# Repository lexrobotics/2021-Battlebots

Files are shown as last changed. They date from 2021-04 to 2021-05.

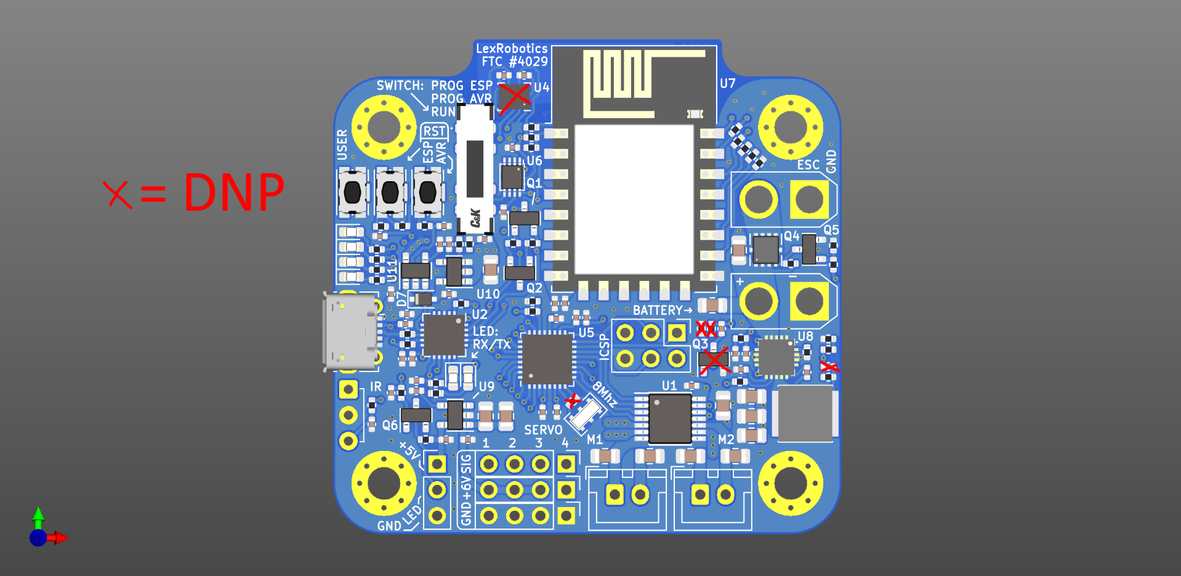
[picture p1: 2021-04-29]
BattlebotsController/BattlebotsController_AssembledView.png

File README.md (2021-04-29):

# 2021-Battlebots

Q: What am I looking at here?

A: 

📦2021-Battlebots \
 ┣ 📂BattlebotsController             `KiCAD files for the battlebots control board hardware` \
 ┣ 📂Code \
 ┃ ┣ 📂peripheralController           `Arduino code for the ATMEGA328P microcontroller` \
 ┃ ┗ 📂wifiController                 `Arduino code for the ESP8266 microcontroller` \
 ┗ 📂OLDVERSION-BattlebotsController  `KiCAD files for the old version of the control board`

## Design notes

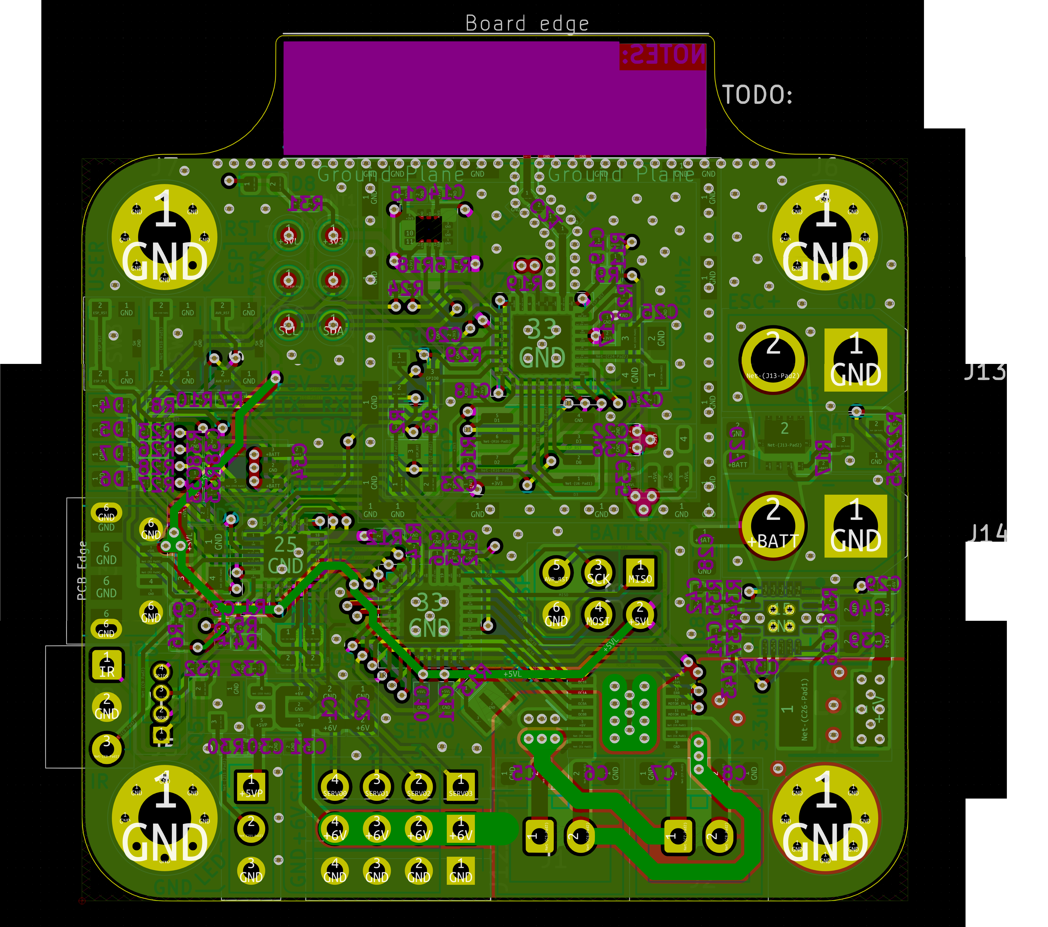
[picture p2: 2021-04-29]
OLDVERSION-BattlebotsController/bottomcopper.png

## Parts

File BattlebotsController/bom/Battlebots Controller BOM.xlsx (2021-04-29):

 | Source: | C:\Users\Anhad\Documents\Kicad\BattlebotsController\BattlebotsController.kicad_sch
 | Date: |  | 2021-04-04 23:49
 | Tool: | Eeschema (5.99.0-10089-gf88d39b4f0)
 | Generator: | C:\Program Files\KiCad\bin\scripting\plugins/bom_csv_grouped_by_value_with_fp.py
 | Component Count: | 149 |  |  |  |  |  |  |  | TOTAL: | 30.91
Item # | *Designator | *Qty | *Mfg Part # | Description / Value | Manufacturer | *Package/Footprint | NOTES | Digikey Part Number | Possible to substitute? | Price (1x) | Price Estimate
1 | C1, C2, C8, C9, C10, C11, C28, C29, C30, C31, C43, C46, C47, | 13 | CL21A106KOQNNNE | 10uf | Samsung Electromechanics | Capacitor_SMD:C_0805_2012Metric | Capacitors must all be >=10V | 1276-1096-1-ND | YES | 0.11 | 1.43
2 | C3, C4, C14, C15, C16, C23, C25, C27, C34, C35, C37, C39, C41, C45, | 14 | GRM155R61C105MA12D | 1uF | Murata Electronics | Capacitor_SMD:C_0402_1005Metric |  | 490-14599-1-ND | YES | 0.1 | 1.4
3 | C5, C6, C7, C17, C18, C19, C20, C21, C22, C24, C26, C32, | 12 | EMF105B7104KVHF | 0.1uF | Taiyo Yuden | Capacitor_SMD:C_0402_1005Metric |  | 587-6563-1-ND | YES | 0.1 | 1.2
4 | C12, C13, | 2 | CC0402GRNPO9BN470 | 47pF | Yageo | Capacitor_SMD:C_0402_1005Metric |  | 311-3741-1-ND | YES | 0.1 | 0.2
5 | C33, | 1 |  | NC |  | Capacitor_SMD:C_0402_1005Metric | DO NOT POPULATE |  |  |  | 0
6 | C36, C40, | 2 | CC0402JRX7R9BB471 | 470pF | Yageo | Capacitor_SMD:C_0402_1005Metric |  | 311-1679-1-ND | YES | 0.1 | 0.2
7 | C38, C44, | 2 | GRM155R71E223JA61D | 22nF | Murata Electronics | Capacitor_SMD:C_0402_1005Metric |  | 490-10699-1-ND | YES | 0.1 | 0.2
8 | C42, | 1 | CL05C390JB51PNC | 39pF | Samsung Electromechanics | Capacitor_SMD:C_0402_1005Metric |  | 1276-6863-1-ND | YES | 0.1 | 0.1
9 | C48, | 1 | CC0402JRX7R9BB392 | 3.9nF | Yageo | Capacitor_SMD:C_0402_1005Metric |  | 311-3771-1-ND | YES | 0.1 | 0.1
10 | D1, D2, D3, D4, D5, D6, | 6 | 150060VS75000 | LED 20mA, 2V | Würth Elektronik | LED_SMD:LED_0603_1608Metric | Green | 732-4980-1-ND | YES | 0.14 | 0.84
11 | D7, | 1 | PMEG4005EJ,115 | Schottky Diode | Nexperia USA Inc. | Diode_SMD:D_SOD-323F | < 0.5V voltage drop | 1727-3877-1-ND | YES | 0.31 | 0.31
12 | J3, | 1 | 1050170001 | USB_B_Micro | Molex | Connector_USB:USB_Micro-B_Molex-105017-0001 |  | WM1399CT-ND | NO | 0.83 | 0.83
13 | L1, | 1 | SRP5030CA-3R3M | 3.3uH | Bourns Incorporated | SRP5030CA:INDPM5355X310N | Shielded | SRP5030CA-3R3MCT-ND | NO | 1.65 | 1.65
14 | Q1, Q2, Q5, Q6, | 4 | MMSS8050-H-TP | S8050 | Micro Commercial Co. | Package_TO_SOT_SMD:SOT-23 | 0.7A Ic, 20V Vce, Low Voltage High Current NPN Transistor, TO-92 | MMSS8050-H-TPMSCT-ND | YES | 0.18 | 0.72
15 | Q3, | 1 | NC (S8050) | Q_NPN_BEC |  | Package_TO_SOT_SMD:SOT-23 | DO NOT POPULATE |  | YES
16 | Q4, | 1 | AONR21307 | P-MOSFET transistor, gate/drain/source | Alpha & Omega Semiconductor | AONR21307:TRANS_AONR21321 |  | 785-1796-1-ND | YES | 0.56 | 0.56
17 | R1, R2, R5, R6, R12, R13, R15, R23, R24, R25, R26, R29, R30, R31, R33, R40, | 16 | RC0402FR-0712KL | 12k | Yageo | Resistor_SMD:R_0402_1005Metric |  | 311-12.0KLRCT-ND | YES | 0.1 | 1.6
18 | R3, R4, R28, R32, R34, | 5 | CRCW0402470RFKEDC | 470 | Vishay Dale | Resistor_SMD:R_0402_1005Metric |  | 541-4072-1-ND | YES | 0.1 | 0.5
19 | R7, R8, | 2 | AC0402FR-0727RL | 27 | Yageo | Resistor_SMD:R_0402_1005Metric |  | YAG5278CT-ND | YES
20 | R9, R10, R11, R14, R16, R18, R19, | 7 | RC0402FR-07270RL | 270 | Yageo | Resistor_SMD:R_0402_1005Metric |  | 311-270LRCT-ND | YES | 0.1 | 0.7
21 | R17, R20, R22, | 3 |  | NC |  | Resistor_SMD:R_0402_1005Metric | DO NOT POPULATE
22 | R21, R35, | 2 | CRCW040218K0FKED | 18k | Vishay Dale | Resistor_SMD:R_0402_1005Metric |  | 541-18.0KLCT-ND | YES | 0.1 | 0.2
23 | R27, R36, R41, | 3 | CRCW04021K00FKEDC | 1k | Vishay Dale | Resistor_SMD:R_0402_1005Metric |  | 541-3961-1-ND | YES | 0.1 | 0.3
24 | R37, | 1 | RC0402FR-0743KL | 43k | Yageo | Resistor_SMD:R_0402_1005Metric |  | 311-43.0KLRCT-ND | YES | 0.1 | 0.1
25 | R38, | 1 | RC0402DR-07100KL | 100k | Yageo | Resistor_SMD:R_0402_1005Metric |  | 13-RC0402DR-07100KLCT-ND | YES | 0.1 | 0.1
26 | R39, | 1 | CRCW04024K64FKED | 4.64k | Vishay Dale | Resistor_SMD:R_0402_1005Metric |  | 541-4.64KLCT-ND | YES | 0.1 | 0.1
27 | SW1, SW2, SW3, | 3 | KMR221GLFS | SPST BUTTON | C&K | Button_Switch_SMD:SW_Push_1P1T-SH_NO_CK_KMR2xxG |  | 401-1427-1-ND | NO | 0.48 | 1.44
28 | SW4, | 1 | JS203011JCQN | DP3T SLIDE | C&K | BattlebotsController:JS203011JCQN | Switch, three position, double pole triple throw, 3 position switch, SP3T | CKN10725CT-ND | NO | 0.65 | 0.65
29 | U1, | 1 | TLE94004EP | Motor Driver | Infineon | Package_SO:Infineon_PG-TSDSO-14-22 |  | TLE94004EPXUMA1CT-ND | NO | 2.07 | 2.07
30 | U2, | 1 | FT231XQ | USB - UART | FTDI, Future Technology Devices International Ltd | Package_DFN_QFN:QFN-20-1EP_4x4mm_P0.5mm_EP2.5x2.5mm | Full Speed USB to Full Handshake UART, QFN-20 | 768-1155-ND | NO | 2.22 | 2.22
31 | U4, | 1 | LSM6DSM | LSM6DSx | STMicroelectronics | Package_LGA:LGA-14_3x2.5mm_P0.5mm_LayoutBorder3x4y | DO NOT POPULATE | 497-16696-1-ND | YES | 2.92 | 2.92
32 | U5, | 1 | ATmega328P-MU | 20MHz, 32kB Flash, 2kB SRAM, 1kB EEPROM, QFN-32 | Microchip Technology | Package_DFN_QFN:QFN-32-1EP_5x5mm_P0.5mm_EP3.1x3.1mm |  | ATMEGA328P-MU-ND | NO | 2.01 | 2.01
33 | U6, | 1 | TXB0102DCU | Level Shifter | Texas Instruments | Package_SO:VSSOP-8_2.4x2.1mm_P0.5mm | 2-Bit Bidirectional Voltage-Level Translator in VSSOP Package With Auto Direction Sensing and ±15-kV ESD Protection | 296-22862-1-ND | NO | 0.76 | 0.76
34 | U7, | 1 | ESP-12F | ESP8266 Module | Ai-Thinker | RF_Module:ESP-12E/F | 802.11 b/g/n Wi-Fi Module |  | NO* |  | 0
35 | U8, | 1 | TPS54821RHLR | 8A Buck Converter | Texas Instruments | TPS54821:IC_TPS54821RHLR |  | 296-29744-1-ND | NO | 2.92 | 2.92
36 | U9, | 1 | MIC5219-5.0YM5 | FIXED 5V!!!! | Microchip Technology | Package_TO_SOT_SMD:SOT-23-5 | 500mA low dropout linear regulator, fixed 5.0V output, SOT-23-5 | 576-2770-1-ND | YES | 0.89 | 0.89
37 | U10, | 1 | SPX3819M5-L | ADJUSTABLE!!!! | MaxLinear Incorporated | Package_TO_SOT_SMD:SOT-23-5 | 500mA Low drop-out regulator, Adjustable, SOT-23-5 | 1016-1873-1-ND | NO | 0.49 | 0.49
38 | U11, | 1 | MIC5219-3.3YM5 | FIXED 3.3V!!!! | Microchip Technology | Package_TO_SOT_SMD:SOT-23-5 | 500mA low dropout linear regulator, fixed 3.3V output, SOT-23-5 | 576-1281-1-ND | YES | 0.93 | 0.93
39 | Y1, | 1 | CSTNE16M0V530000R0 | 16M resonator | Murata Electronics | Crystal:Resonator_SMD_muRata_CSTxExxV-3Pin_3.0x1.1mm | Three pin ceramic resonator | 490-17948-1-ND | YES | 0.27 | 0.27
40
41
42
 | NOT POPULATED / THRU HOLE | PCBWAY - IGNORE
Item # | *Designator | *Qty | *Mfg Part # | Description / Value | Manufacturer | *Package/Footprint | NOTES | Digikey Part Number | Possible to substitute with another equivalent part? | Price (1x) | Unit Price
43 | TP1, TP2, TP3, TP4, TP5, TP6, TP7, TP8, TP9, TP10, TP11, TP12, TP13, | 13 |  | TestPoint_Flag | TestPoint_Flag | TestPoint:TestPoint_Pad_D1.5mm | DO NOT POPULATE
44 | JP1, JP2, JP3, | 3 |  | Jumper_NC_Small | Jumper_NC_Small | Jumper:SolderJumper-2_P1.3mm_Bridged_RoundedPad1.0x1.5mm | DO NOT POPULATE
45 | MH1, MH2, MH3, MH4, | 4 |  | MOUNTING_HOLE | Conn_01x01 | MountingHole:MountingHole_3.2mm_M3_Pad_Via | DO NOT POPULATE
46 | J4, | 1 |  | ICSP | Conn_02x03_Odd_Even | Connector_PinHeader_2.54mm:PinHeader_2x03_P2.54mm_Vertical | DO NOT POPULATE
47 | J5, | 1 |  | SIG | Conn_01x04 | Connector_PinHeader_2.54mm:PinHeader_1x04_P2.54mm_Vertical | DO NOT POPULATE
48 | J6, | 1 |  | +6V | Conn_01x04 | Connector_PinHeader_2.54mm:PinHeader_1x04_P2.54mm_Vertical | DO NOT POPULATE
49 | J7, | 1 |  | GND | Conn_01x04 | Connector_PinHeader_2.54mm:PinHeader_1x04_P2.54mm_Vertical | DO NOT POPULATE
50 | J8, | 1 |  | ESC | Conn_01x02 | Connector_AMASS:AMASS_XT30U-M_1x02_P5.0mm_Vertical | DO NOT POPULATE
51 | J9, | 1 |  | BATTERY | Conn_01x02 | Connector_AMASS:AMASS_XT30U-M_1x02_P5.0mm_Vertical | DO NOT POPULATE
52 | J10, | 1 |  | WS2812b | Conn_01x03 | Connector_PinHeader_2.54mm:PinHeader_1x03_P2.54mm_Vertical | DO NOT POPULATE
53 | J1, | 1 | B2B-XH-A-M(LF)(SN) | DRIVE_MOTOR_R | Conn_01x02 | Connector_JST:JST_XH_B2B-XH-A_1x02_P2.50mm_Vertical | DO NOT POPULATE
54 | J2, | 1 | B2B-XH-A-M(LF)(SN) | DRIVE_MOTOR_L | Conn_01x02 | Connector_JST:JST_XH_B2B-XH-A_1x02_P2.50mm_Vertical | DO NOT POPULATE
55 | U3, | 1 | TSOP382xx | TSOP382xx | OptoDevice:Vishay_MINICAST-3Pin | Photo Modules for PCM Remote Control Systems | DO NOT POPULATE |  | YES
56
57
58 | TOTAL NC/THRU-HOLE PARTS | 30
59
60

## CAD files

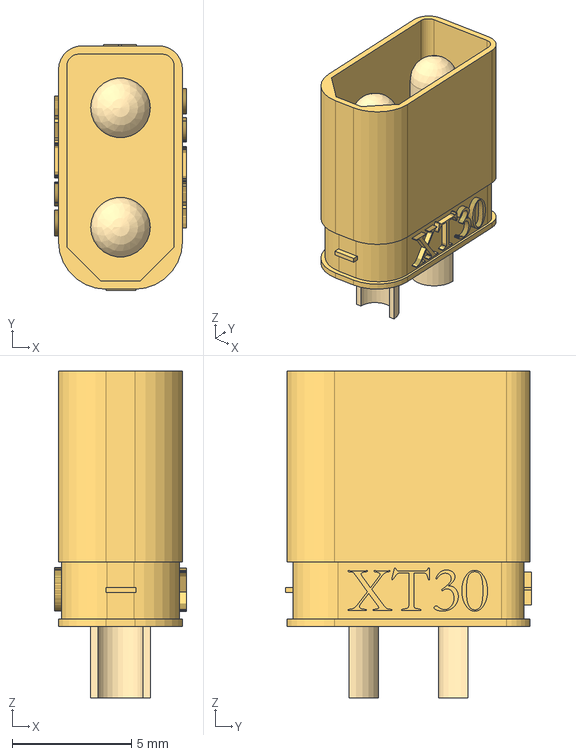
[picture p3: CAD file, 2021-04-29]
BattlebotsController/3D/XT30-male.step
5.54 x 10.3 x 13.7 mm

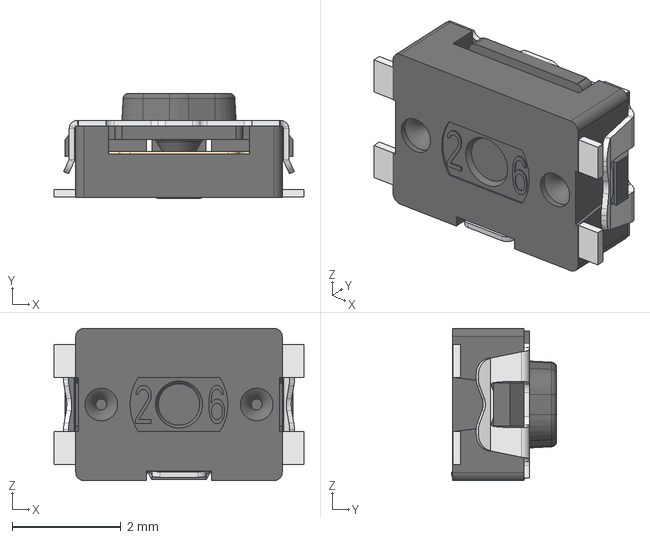
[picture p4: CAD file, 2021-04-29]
BattlebotsController/3D/KMR211GLFS.step
4.60 x 1.94 x 2.80 mm

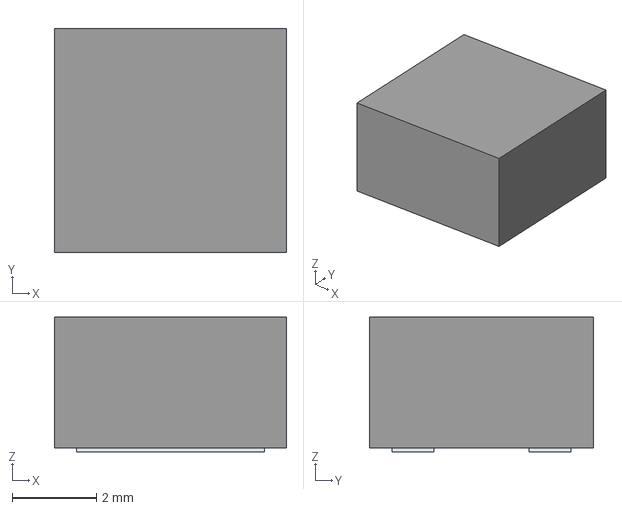
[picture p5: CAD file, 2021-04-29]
BattlebotsController/3D/SRP5030CA.stp
5.50 x 5.30 x 3.20 mm
Pins

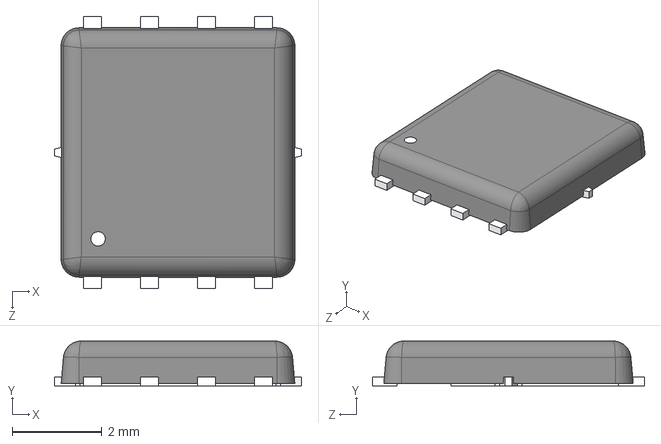
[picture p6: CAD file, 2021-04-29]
BattlebotsController/3D/MOSFET_AONR.STEP
5.50 x 1.00 x 6.05 mm

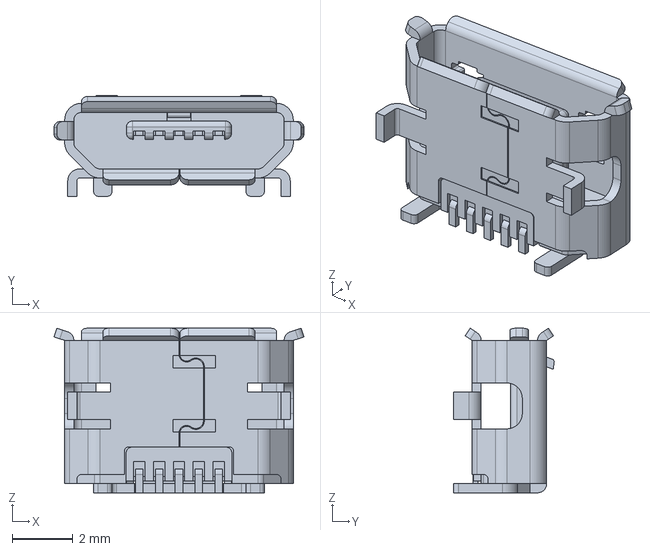
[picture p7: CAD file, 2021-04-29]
BattlebotsController/3D/Molex_1050170001.stp
8.20 x 3.30 x 5.40 mm

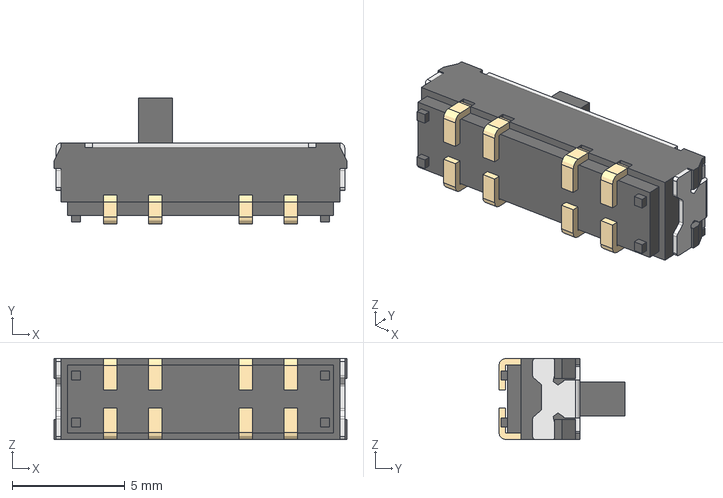
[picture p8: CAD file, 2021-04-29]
BattlebotsController/3D/JS203011JCQN.step
13.0 x 5.60 x 3.60 mm

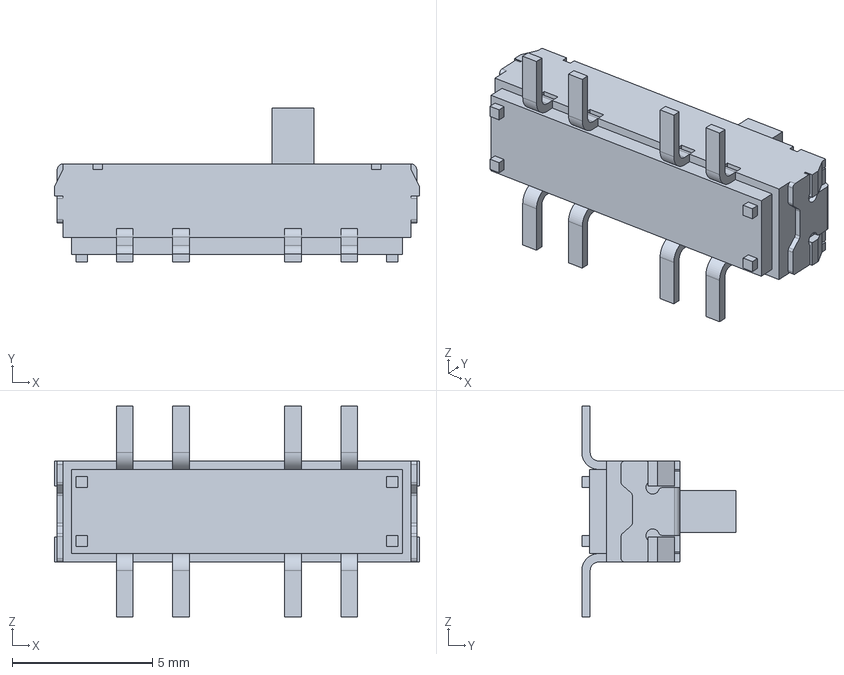
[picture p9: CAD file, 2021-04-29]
BattlebotsController/3D/JS203011SCQN.stp
13.0 x 5.50 x 7.50 mm

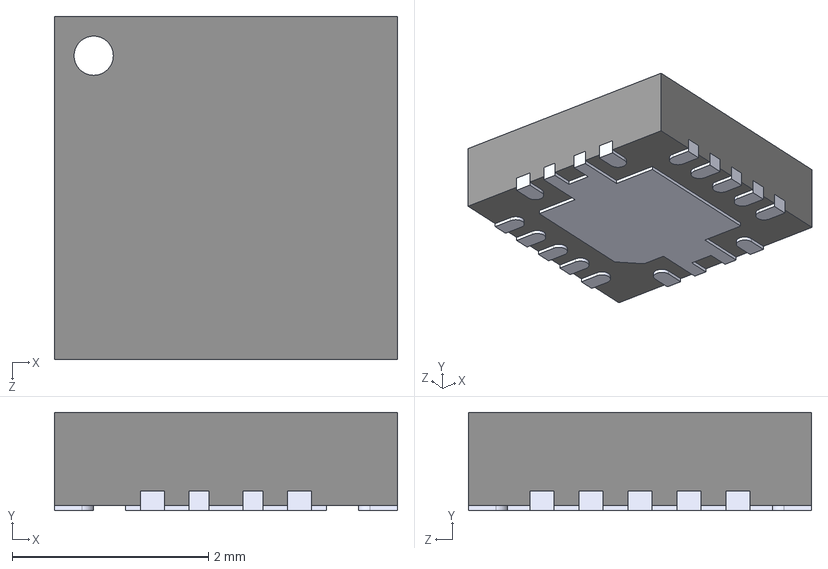
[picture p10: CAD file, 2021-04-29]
BattlebotsController/3D/TPS54821RHLR--3DModel-STEP-56544.STEP
3.50 x 1.00 x 3.50 mm

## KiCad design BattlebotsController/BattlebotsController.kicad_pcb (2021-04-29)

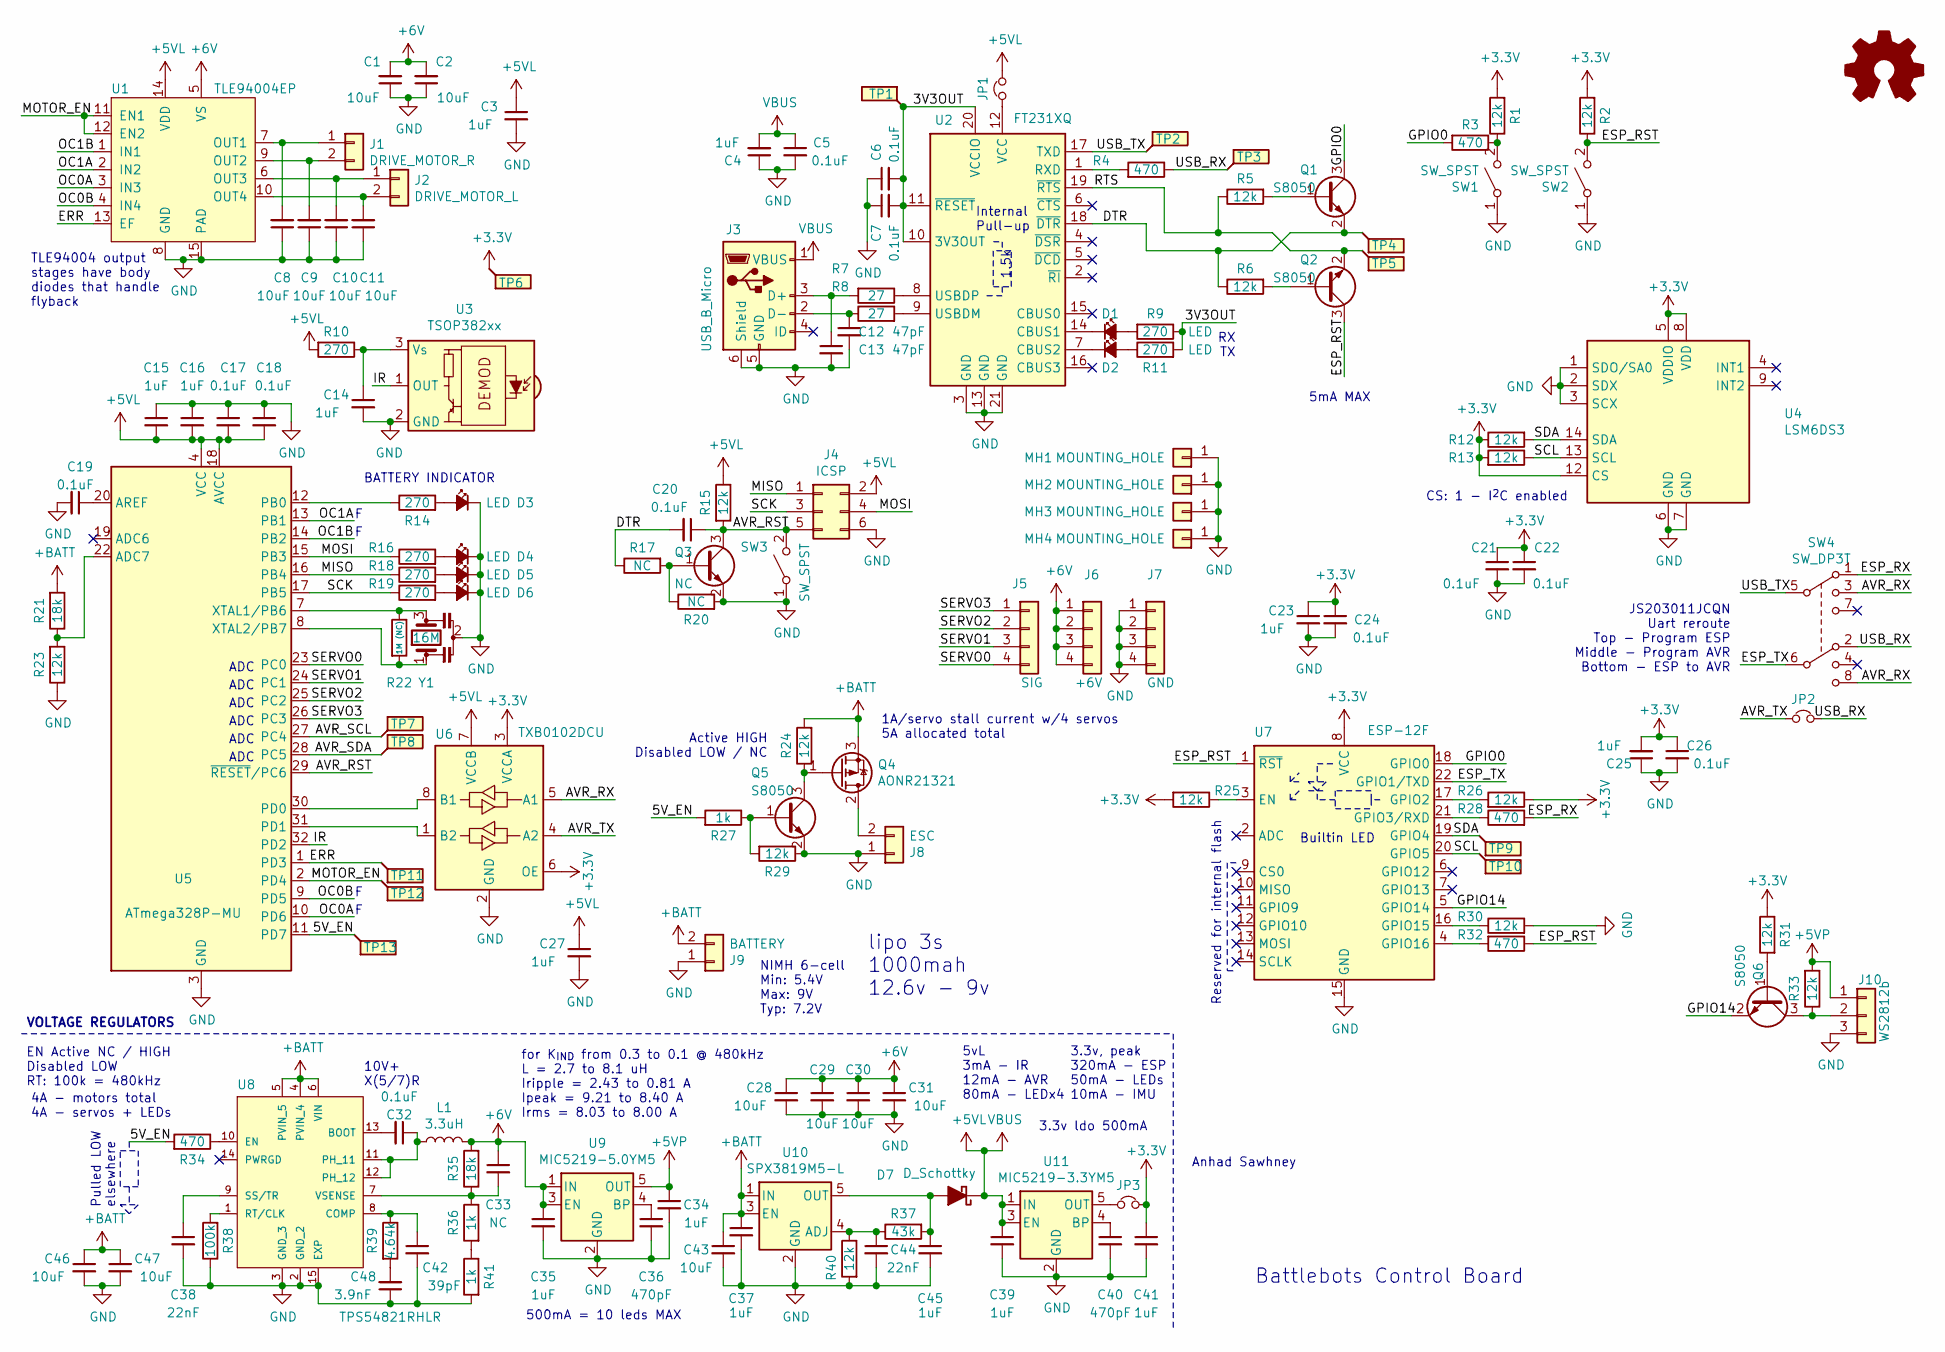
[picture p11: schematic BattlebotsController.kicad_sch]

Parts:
C1, C2, C8, C9, C10, C11, C28, C29, C30, C31, C43, C46, C47: 10uF; C_0805_2012Metric
C3, C4, C14, C15, C16, C23, C25, C27, C34, C35, C37, C39, C41, C45: 1uF; C_0402_1005Metric
C5, C6, C7, C17, C18, C19, C20, C21, C22, C24, C26, C32: 0.1uF; C_0402_1005Metric
C12, C13: 47pF; C_0402_1005Metric
C33: NC; C_0402_1005Metric
C36, C40: 470pF; C_0402_1005Metric
C38, C44: 22nF; C_0402_1005Metric
C42: 39pF; C_0402_1005Metric
C48: 3.9nF; C_0402_1005Metric
D1, D2, D3, D4, D5, D6: LED; LED_0603_1608Metric
D7: D_Schottky; D_SOD-323F
J1: DRIVE_MOTOR_R; JST_XH_B2B-XH-A_1x02_P2.50mm_Vertical
J2: DRIVE_MOTOR_L; JST_XH_B2B-XH-A_1x02_P2.50mm_Vertical
J3: USB_B_Micro; USB_Micro-B_Molex-105017-0001
J4: ICSP; PinHeader_2x03_P2.54mm_Vertical
J5: SIG; PinHeader_1x04_P2.54mm_Vertical
J6: +6V; PinHeader_1x04_P2.54mm_Vertical
J7: GND; PinHeader_1x04_P2.54mm_Vertical
J8: ESC; AMASS_XT30U-M_1x02_P5.0mm_Vertical
J9: BATTERY; AMASS_XT30U-M_1x02_P5.0mm_Vertical
J10: WS2812b; PinHeader_1x03_P2.54mm_Vertical
JP1, JP2, JP3: Jumper_NC_Small; SolderJumper-2_P1.3mm_Bridged_RoundedPad1.0x1.5mm
L1: 3.3uH; INDPM5355X310N
MH1, MH2, MH3, MH4: MOUNTING_HOLE; MountingHole_3.2mm_M3_Pad_Via
Q1, Q2, Q5, Q6: S8050; SOT-23
Q3: NC; SOT-23
Q4: AONR21321; TRANS_AONR21321
R1, R2, R5, R6, R12, R13, R15, R23, R24, R25, R26, R29, R30, R31, R33, R40: 12k; R_0402_1005Metric
R3, R4, R28, R32, R34: 470; R_0402_1005Metric
R7, R8: 27; R_0402_1005Metric
R9, R10, R11, R14, R16, R18, R19: 270; R_0402_1005Metric
R17, R20: NC; R_0402_1005Metric
R21, R35: 18k; R_0402_1005Metric
R22: 1M (NC); R_0402_1005Metric
R27, R36, R41: 1k; R_0402_1005Metric
R37: 43k; R_0402_1005Metric
R38: 100k; R_0402_1005Metric
R39: 4.64k; R_0402_1005Metric
SW1, SW2, SW3: SW_SPST; SW_Push_1P1T-SH_NO_CK_KMR2xxG
SW4: SW_DP3T; JS203011JCQN
TP1, TP2, TP3, TP4, TP5, TP6, TP7, TP8, TP9, TP10, TP11, TP12, TP13: TestPoint_Flag; TestPoint_Pad_D1.5mm
U1: TLE94004EP; Infineon_PG-TSDSO-14-22
U2: FT231XQ; QFN-20-1EP_4x4mm_P0.5mm_EP2.5x2.5mm
U3: TSOP382xx; Vishay_MINICAST-3Pin
U4: LSM6DS3; LGA-14_3x2.5mm_P0.5mm_LayoutBorder3x4y
U5: ATmega328P-MU; QFN-32-1EP_5x5mm_P0.5mm_EP3.1x3.1mm
U6: TXB0102DCU; VSSOP-8_2.4x2.1mm_P0.5mm
U7: ESP-12F; ESP-12E
U8: TPS54821RHLR; IC_TPS54821RHLR
U9: MIC5219-5.0YM5; SOT-23-5
U10: SPX3819M5-L; SOT-23-5
U11: MIC5219-3.3YM5; SOT-23-5
Y1: 16M; Resonator_SMD_Murata_CSTxExxV-3Pin_3.0x1.1mm

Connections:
+3V3: C21.1, C22.1, C23.1, C24.1, C25.2, C26.1, C41.1, JP3.2, R1.2, R2.2, R12.1, R13.2, R25.2, R26.1, R31.1, TP6.1, U4.5 (VDDIO), U4.8 (VDD), U4.12 (CS), U6.3 (VCCA), U6.6 (OE), U7.8 (VCC)
+5VL: C3.1, C4.2, C5.1, C15.2, C16.2, C17.2, C18.2, C27.1, C39.1, D7.1 (K), J3.1 (VBUS), J4.2, JP1.2, R10.2, R15.1, U1.14 (VDD), U5.4 (VCC), U5.6 (VCC), U5.18 (AVCC), U6.7 (VCCB), U11.1 (IN), U11.3 (EN)
+5VP: C34.1, J10.1, R33.2, U9.5 (OUT)
+6V: C1.2, C2.2, C28.1, C29.1, C30.1, C31.1, C33.1, C35.1, J6.1, J6.2, J6.3, J6.4, L1.2, R35.2, U1.5 (VS), U9.1 (IN), U9.3 (EN)
+BATT: C37.1, C43.1, C46.1, C47.1, J9.2, Q4.3 (S), R21.2, R24.2, U8.4 (PVIN_4), U8.5 (PVIN_5), U8.6 (VIN), U10.1 (IN), U10.3 (EN)
/3V3OUT: C6.2, C7.2, R9.1, R11.2, TP1.1, U2.10 (3V3OUT), U2.11 (~RESET), U2.20 (VCCIO)
/5V_EN: R27.2, R34.2, TP13.1, U5.11 (PD7)
/AVR_RST: C20.1, J4.5, Q3.3 (C), R15.2, SW3.2 (B), U5.29 (~RESET~/PC6)
/AVR_RX: SW4.3, SW4.8, U6.5 (A1)
/AVR_SCL: TP7.1, U5.27 (PC4)
/AVR_SDA: TP8.1, U5.28 (PC5)
/AVR_TX: JP2.1, U6.4 (A2)
/DTR: C20.2, Q1.2 (E), R6.1, R17.1, TP4.1, U2.18 (~DTR)
/ERR: TP11.1, U1.13 (EF), U5.1 (PD3)
/ESP_RST: Q2.3 (C), R2.1, R32.1, SW2.2 (B), U7.1 (~RST)
/ESP_RX: R28.2, SW4.1
/ESP_TX: SW4.6, U7.22 (GPIO1/TXD)
/GPIO0: Q1.3 (C), R3.2, U7.18 (GPIO0)
/GPIO14: Q6.2 (E), U7.5 (GPIO14)
/IR: U3.1 (OUT), U5.32 (PD2)
/MISO: J4.1, R18.1, U5.16 (PB4)
/MOSI: J4.4, R16.1, U5.15 (PB3)
/MOTOR_EN: TP12.1, U1.11 (EN1), U1.12 (EN2), U5.2 (PD4)
/OC0A: U1.3 (IN3), U5.10 (PD6)
/OC0B: U1.4 (IN4), U5.9 (PD5)
/OC1A: U1.2 (IN2), U5.13 (PB1)
/OC1B: U1.1 (IN1), U5.14 (PB2)
/RTS: Q2.2 (E), R5.1, TP5.1, U2.19 (~RTS)
/SCK: J4.3, R19.1, U5.17 (PB5)
/SCL: R13.1, TP10.1, U4.13 (SCL), U7.20 (GPIO5)
/SDA: R12.2, TP9.1, U4.14 (SDA), U7.19 (GPIO4)
/SERVO0: J5.4, U5.23 (PC0)
/SERVO1: J5.3, U5.24 (PC1)
/SERVO2: J5.2, U5.25 (PC2)
/SERVO3: J5.1, U5.26 (PC3)
/USB_RX: JP2.2, R4.1, SW4.2, TP3.1
/USB_TX: SW4.5, TP2.1, U2.17 (TXD)
GND: C1.1, C2.1, C3.2, C4.1, C5.2, C6.1, C7.1, C8.1, C9.1, C10.1, C11.1, C12.2, C13.2, C14.2, C15.1, C16.1, C17.1, C18.1, C19.2, C21.2, C22.2, C23.2, C24.2, C25.1, C26.2, C27.2, C28.2, C29.2, C30.2, C31.2, C34.2, C35.2, C36.2, C37.2, C38.2, C39.2, C40.2, C41.2, C42.2, C43.2, C44.2, C45.2, C46.2, C47.2, C48.1, D3.1 (K), D4.1 (K), D5.1 (K), D6.1 (K), J3.5 (GND), J3.6 (Shield), J4.6, J7.1, J7.2, J7.3, J7.4, J8.1, J9.1, J10.3, MH1.1, MH2.1, MH3.1, MH4.1, Q3.2 (E), Q5.2 (E), R20.2, R23.1, R29.1, R30.2, R38.1, R40.2, R41.2, SW1.1 (A), SW2.1 (A), SW3.1 (A), U1.8 (GND), U1.15 (PAD), U2.3 (GND), U2.13 (GND), U2.21 (GND), U3.2 (GND), U4.1 (SDO/SA0), U4.2 (SDX), U4.3 (SCX), U4.6 (GND), U4.7 (GND), U5.3 (GND), U5.5 (GND), U5.21 (GND), U5.33 (GND), U6.2 (GND), U7.15 (GND), U8.2 (GND_2), U8.3 (GND_3), U8.15 (EXP), U9.2 (GND), U10.2 (GND), U11.2 (GND), Y1.2
unnamed: C8.2, J1.1, U1.7 (OUT1)
unnamed: C9.2, J1.2, U1.9 (OUT2)
unnamed: C10.2, J2.1, U1.6 (OUT3)
unnamed: C11.2, J2.2, U1.10 (OUT4)
unnamed: C12.1, J3.2 (D-), R8.1
unnamed: C13.1, J3.3 (D+), R7.2
unnamed: C19.1, U5.20 (AREF)
unnamed: C32.1, L1.1, U8.11 (PH_11), U8.12 (PH_12)
unnamed: C32.2, U8.13 (BOOT)
unnamed: C33.2, R35.1, R36.1, U8.7 (VSENSE)
unnamed: C36.1, U9.4 (BP)
unnamed: C38.1, U8.9 (SS/TR)
unnamed: C40.1, U11.4 (BP)
unnamed: C42.1, R39.1, U8.8 (COMP)
unnamed: C44.1, R37.1, R40.1, U10.4 (ADJ)
unnamed: C45.1, D7.2 (A), R37.2, U10.5 (OUT)
unnamed: C48.2, R39.2
unnamed: D1.1 (K), U2.14 (CBUS1)
unnamed: D1.2 (A), R9.2
unnamed: D2.1 (K), U2.7 (CBUS2)
unnamed: D2.2 (A), R11.1
unnamed: D3.2 (A), R14.2
unnamed: D4.2 (A), R16.2
unnamed: D5.2 (A), R18.2
unnamed: D6.2 (A), R19.2
unnamed: J8.2, Q4.2 (D)
unnamed: J10.2, Q6.3 (C), R33.1
unnamed: JP1.1, U2.12 (VCC)
unnamed: JP3.1, U11.5 (OUT)
unnamed: Q1.1 (B), R5.2
unnamed: Q2.1 (B), R6.2
unnamed: Q3.1 (B), R17.2, R20.1
unnamed: Q4.1 (G), Q5.3 (C), R24.1
unnamed: Q5.1 (B), R27.1, R29.2
unnamed: Q6.1 (B), R31.2
unnamed: R1.1, R3.1, SW1.2 (B)
unnamed: R4.2, U2.1 (RXD)
unnamed: R7.1, U2.8 (USBDP)
unnamed: R8.2, U2.9 (USBDM)
unnamed: C14.1, R10.1, U3.3 (Vs)
unnamed: R14.1, U5.12 (PB0)
unnamed: R21.1, R23.2, U5.22 (ADC7)
unnamed: R22.1, U5.7 (XTAL1/PB6), Y1.3
unnamed: R22.2, U5.8 (XTAL2/PB7), Y1.1
unnamed: R25.1, U7.3 (EN)
unnamed: R26.2, U7.17 (GPIO2)
unnamed: R28.1, U7.21 (GPIO3/RXD)
unnamed: R30.1, U7.16 (GPIO15)
unnamed: R32.2, U7.4 (GPIO16)
unnamed: R34.1, U8.10 (EN)
unnamed: R36.2, R41.1
unnamed: R38.2, U8.1 (RT/CLK)
unnamed: U5.30 (PD0), U6.8 (B1)
unnamed: U5.31 (PD1), U6.1 (B2)

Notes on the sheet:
VOLTAGE REGULATORS
EN Active NC / HIGH Disabled LOW RT: 100k = 480kHz
TLE94004 output stages have body diodes that handle flyback
4A - motors total 4A - servos + LEDs
Pulled LOW elsewhere
ADC
BATTERY INDICATOR
10V+ X(5/7)R
for K_{IND} from 0.3 to 0.1 @ 480kHz L = 2.7 to 8.1 uH Iripple = 2.43 to 0.81 A Ipeak = 9.21 to 8.40 A Irms = 8.03 to 8.00 A
500mA = 10 leds MAX
NIMH 6-cell Min: 5.4V Max: 9V Typ: 7.2V
Active HIGH Disabled LOW / NC
lipo 3s 1000mah 12.6v - 9v
1A/servo stall current w/4 servos 5A allocated total
5vL 3mA - IR 12mA - AVR 80mA - LEDx4
Internal Pull-up
1.5k
3.3v ldo 500mA
3.3v, peak 320mA - ESP 50mA - LEDs 10mA - IMU
Anhad Sawhney
RX TX
Reserved for internal flash
Battlebots Control Board
Builtin LED
5mA MAX
CS: 1 - I^{2}C enabled
JS203011JCQN Uart reroute Top - Program ESP Middle - Program AVR Bottom - ESP to AVR

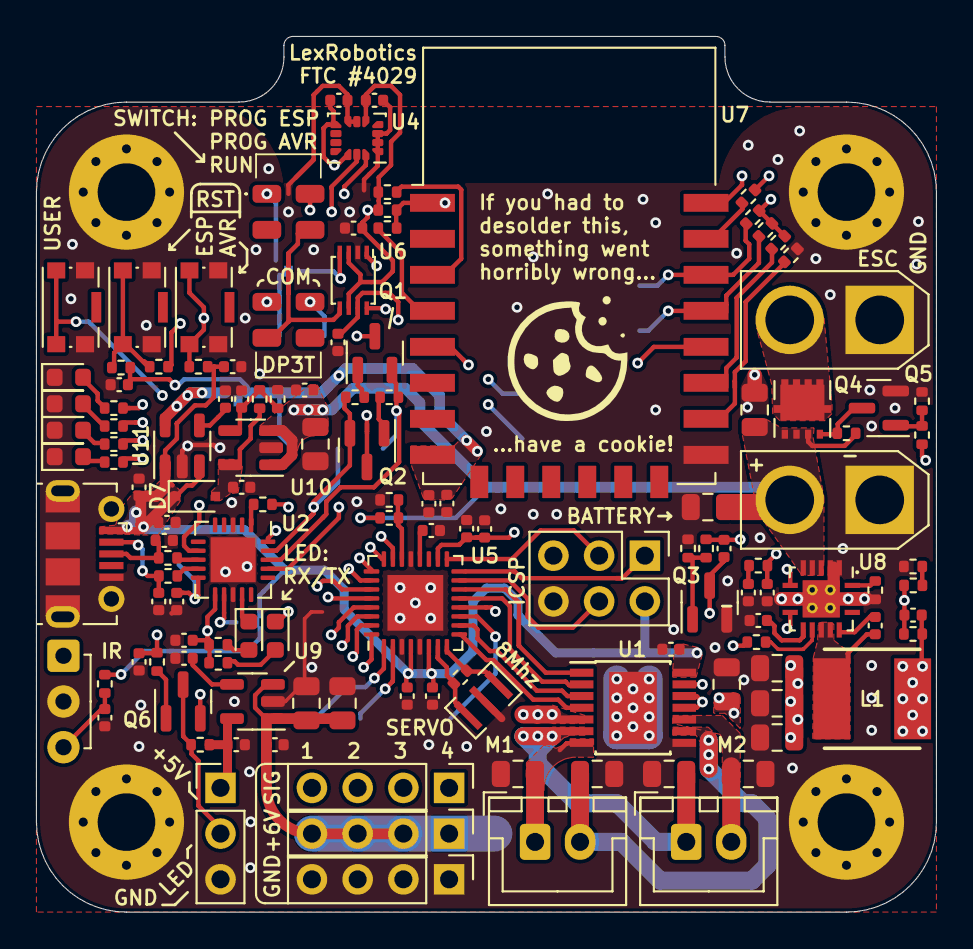
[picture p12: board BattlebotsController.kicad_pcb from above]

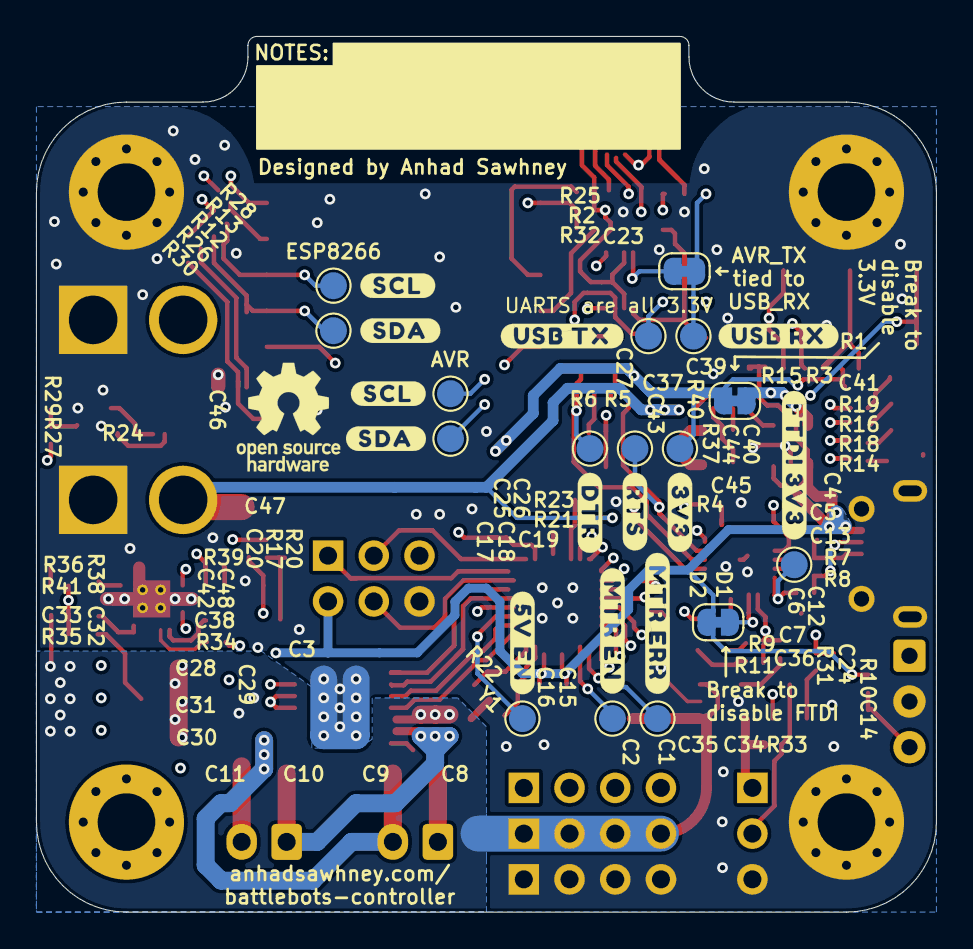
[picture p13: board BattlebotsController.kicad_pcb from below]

Board: 4 copper layers, 50.0 x 48.6 mm, 149 parts (16 on the bottom side), 92 nets.

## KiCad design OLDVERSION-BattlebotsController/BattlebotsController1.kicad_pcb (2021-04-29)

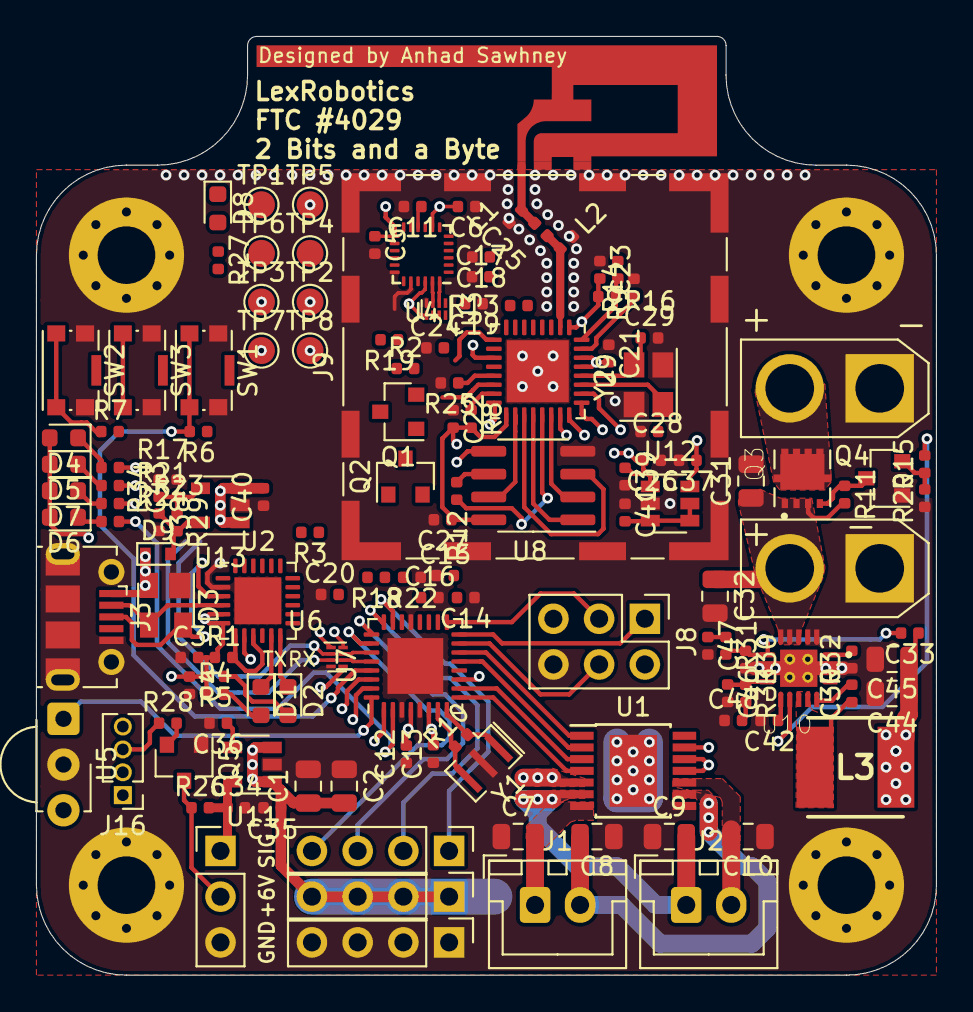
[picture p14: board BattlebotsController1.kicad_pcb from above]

Board: 4 copper layers, 50.0 x 52.1 mm, 142 parts (0 on the bottom side), 96 nets.

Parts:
ANT1: Inverted F; SWRU120B
C1, C2: 10uf; C_0805_2012Metric
C3, C26, C37, C39: 1uF; C_0402_1005Metric
C4, C5, C6, C11, C17, C18, C19, C20, C27: 0.1uF; C_0402_1005Metric
C7, C8, C9, C10, C31, C32, C44, C45: 10uF; C_0805_2012Metric
C12, C13, C21, C22, C41: 1uf; C_0402_1005Metric
C14, C15, C16, C23, C24: 0.1uf; C_0402_1005Metric
C25: 5.6pf; C_0402_1005Metric
C28, C29: NC; C_0402_1005Metric
C30, C42: 10uF; C_0402_1005Metric
C33, C35, C47: 330pf; C_0402_1005Metric
C34, C38, C40: 2.2uf; C_0402_1005Metric
C36, C43: 470pf; C_0402_1005Metric
C46: 14pf; C_0402_1005Metric
C48: 33nf; C_0402_1005Metric
D1: RXLED; LED_0603_1608Metric
D2: TXLED; LED_0603_1608Metric
D3: SP0503BAHT; SOT-143
D4, D5, D6, D7: LED; LED_0603_1608Metric
D8: ESP_LED; LED_0603_1608Metric
D9: MSK4005; D_SOD-523
J1: DRIVE_MOTOR_R; JST_XH_B2B-XH-A_1x02_P2.50mm_Vertical
J2: DRIVE_MOTOR_L; JST_XH_B2B-XH-A_1x02_P2.50mm_Vertical
J3: USB_B_Micro; USB_Micro-B_Molex-105017-0001
J4, J5, J6, J7: MOUNTING_HOLE; MountingHole_3.2mm_M3_Pad_Via
J8: ICSP; PinHeader_2x03_P2.54mm_Vertical
J9: RF_SHIELD; Wuerth_36103205_20x20mm
J10: SIG; PinHeader_1x04_P2.54mm_Vertical
J11: +6V; PinHeader_1x04_P2.54mm_Vertical
J12: GND; PinHeader_1x04_P2.54mm_Vertical
J13: ESC; AMASS_XT30U-M_1x02_P5.0mm_Vertical
J14: BATTERY; AMASS_XT30U-M_1x02_P5.0mm_Vertical
J15: WS2812b; PinHeader_1x03_P2.54mm_Vertical
J16: LED_DMA; PinHeader_1x04_P1.27mm_Vertical
L1, L2: NC; L_0402_1005Metric
L3: 3.3uH; INDPM5355X310N
Q1, Q2, Q4, Q5: S8050; SOT-23
Q3: Q_PMOS_GDS; TRANS_AONR21321
R1, R15: 1k; R_0402_1005Metric
R2, R3, R6, R7, R8, R11, R13, R14, R16, R20, R25, R28: 12k; R_0402_1005Metric
R4, R5, R17, R21, R23, R24, R27: 270; R_0402_1005Metric
R9: 470; R_0402_1005Metric
R10: 1M; R_0402_1005Metric
R12: 200; R_0402_1005Metric
R18: 56k; R_0402_1005Metric
R19: 499; R_0402_1005Metric
R22: 36k; R_0402_1005Metric
R26: 10k; R_0402_1005Metric
R29: 150k; R_0402_1005Metric
R30, R31, R33: 365k; R_0402_1005Metric
R32: 100k; R_0402_1005Metric
R34: 43k; R_0402_1005Metric
SW1, SW2, SW3: SW_SPST; SW_Push_1P1T-SH_NO_CK_KMR2xxG
TP1, TP2, TP3, TP4, TP5, TP6, TP7, TP8: TestPoint_Flag; TestPoint_Pad_D1.5mm
U1: TLE94004EP; Infineon_PG-TSDSO-14-22
U2: CP2102N-A01-GQFN24; QFN-24-1EP_4x4mm_P0.5mm_EP2.6x2.6mm
U3, U6: TXS0102DQE; X2SON-8_1.4x1mm_P0.35mm
U4: ICM-20948; InvenSense_QFN-24_3x3mm_P0.4mm
U5: TSOP382xx; Vishay_MINICAST-3Pin
U7: ATmega328P-MU; QFN-32-1EP_5x5mm_P0.5mm_EP3.1x3.1mm
U8: AT25SF321B-SSHB-T; SOIC-8_3.9x4.9mm_P1.27mm
U9: ESP8266EX; QFN-32-1EP_5x5mm_P0.5mm_EP3.45x3.45mm
U10: TPS54821RHLR; IC_TPS54821RHLR
U11: MIC5219-5.0YM5; SOT-23-5
U12: AP7312-1833W6-7; SOT-23-6
U13: SPX3819M5-L; SOT-23-5
Y1: 16M; Resonator_SMD_muRata_CSTxExxV-3Pin_3.0x1.1mm
Y2: 26M; Crystal_SMD_SeikoEpson_TSX3225-4Pin_3.2x2.5mm

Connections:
+1V8: C5.1, C6.2, C17.2, C18.1, C37.1, TP4.1, U3.1, U3.5, U4.8, U4.13, U4.22, U12.6
+3V3: C3.2, C4.1, C19.2, C21.2, C22.2, C23.2, C24.2, C26.2, C27.1, C39.1, R1.1, R4.1, R5.2, R7.2, R8.2, R13.1, R16.1, R27.2, TP5.1, U2.5, U2.6, U3.8, U6.1, U6.5, U8.8, U9.1, U9.3, U9.4, U9.5, U9.11, U9.17, U9.29, U9.30, U12.1
+5VL: C12.2, C13.2, C14.2, C15.2, C20.2, C41.2, D3.2, D9.1, J3.1, J8.2, R6.1, TP1.1, U1.14, U2.8, U5.3, U6.8, U7.4, U7.6, U7.18, U12.3, U12.4, U12.5
+5VP: C34.1, D4.2, D5.2, D6.2, D7.2, J15.1, R26.2, U11.5
+6V: C1.1, C2.2, C33.1, C35.1, C44.1, C45.1, J11.1, J11.2, J11.3, J11.4, L3.2, U1.5, U11.1, U11.3
+BATT: C31.1, C32.1, C40.2, J14.2, Q3.3, R11.2, R18.2, U10.4, U10.5, U10.6, U13.1, U13.3
/5V_EN: R15.2, TP6.1, U7.31, U10.10
/AVR_RST: J8.5, R6.2, SW1.2, U7.29
/AVR_SCL: TP8.1, U6.6, U7.28
/AVR_SDA: TP7.1, U6.7, U7.27
/D0: U8.2, U9.22
/D1: U8.5, U9.23
/D2: U8.7, U9.18
/D3: U8.3, U9.19
/ERR: U1.13, U7.1
/ESP_RST: Q2.3, R9.1, R16.2, U9.32
/FTDI_RX_ESP_TX: R19.2, TP2.1, U2.20
/FTDI_TX_ESP_RX: J16.1, TP3.1, U2.21
/GPIO0: Q1.3, R8.1, SW3.2, U9.15
/GPIO5: J16.4, U9.24
/GPIO16: R7.1, R9.2, SW2.2, U9.8
/IR: U5.1, U7.32
/MISO: J8.1, R17.1, U7.16
/MOSI: J8.4, R21.1, U7.15
/MOTOR_EN: U1.11, U1.12, U7.30
/OC0A: U1.3, U7.10
/OC0B: U1.4, U7.9
/OC1A: U1.2, U7.13
/OC1B: U1.1, U7.14
/SCK: J8.3, U7.17
/SCL: U3.6, U6.3, U9.9
/SDA: U3.7, U6.2, U9.14
/SERVO0: J10.1, U7.23
/SERVO1: J10.2, U7.24
/SERVO2: J10.3, U7.25
/SERVO3: J10.4, U7.26
/U0RXD: J16.2, U9.25
GND: ANT1.2, C1.2, C2.1, C3.1, C4.2, C5.2, C6.1, C7.1, C8.1, C9.1, C10.1, C11.2, C12.1, C13.1, C14.1, C15.1, C16.2, C17.1, C18.2, C19.1, C20.1, C21.1, C22.1, C23.1, C24.1, C26.1, C27.2, C28.1, C29.1, C31.2, C32.2, C34.2, C35.2, C36.2, C37.2, C38.2, C39.2, C40.1, C41.1, C42.2, C43.2, C44.2, C45.2, C46.2, C47.2, C48.1, D3.1, J3.5, J3.6, J4.1, J5.1, J6.1, J7.1, J8.6, J9.1, J12.1, J12.2, J12.3, J12.4, J13.1, J14.1, J15.3, L1.2, L2.2, Q4.1, Q5.1, R14.2, R20.1, R22.1, R25.2, R30.2, R32.1, R34.2, SW1.1, SW2.1, SW3.1, U1.8, U1.15, U2.2, U2.25, U3.4, U4.9, U4.18, U4.20, U5.2, U6.4, U7.3, U7.5, U7.21, U7.33, U8.4, U9.33, U10.2, U10.3, U10.15, U10.16, U10.17, U10.18, U10.19, U11.2, U12.2, U13.2, Y1.2, Y2.2, Y2.4
unnamed: ANT1.1, C25.2, L1.1
unnamed: C7.2, J1.1, U1.7
unnamed: C8.2, J1.2, U1.9
unnamed: C9.2, J2.1, U1.6
unnamed: C10.2, J2.2, U1.10
unnamed: C11.1, U4.10
unnamed: C16.1, U7.20
unnamed: C25.1, L2.1, U9.2
unnamed: C28.2, U9.27, Y2.1
unnamed: C29.2, U9.28, Y2.3
unnamed: C30.1, L3.1, U10.11, U10.12
unnamed: C30.2, U10.13
unnamed: C33.2, R30.1, R31.2, U10.7
unnamed: C36.1, U11.4
unnamed: C38.1, D9.2, R29.2, U13.5
unnamed: C42.1, U10.9
unnamed: C43.1, R29.1, R34.1, U13.4
unnamed: C46.1, R33.1, U10.8
unnamed: C47.1, R31.1
unnamed: C48.2, R33.2
unnamed: D1.1, U2.11
unnamed: D1.2, R4.2
unnamed: D2.1, U2.12
unnamed: D2.2, R5.1
unnamed: D3.3, J3.2, U2.4
unnamed: D3.4, J3.3, U2.3
unnamed: D4.1, R17.2
unnamed: D5.1, R21.2
unnamed: D6.1, R23.2
unnamed: D7.1, R24.2
unnamed: D8.1, U9.16
unnamed: D8.2, R27.1
unnamed: J13.2, Q3.2
unnamed: J15.2, Q5.3, R26.1
unnamed: J16.3, R28.1
unnamed: Q1.1, R3.1, U2.23
unnamed: Q1.2, R2.2
unnamed: Q2.1, R2.1, U2.19
unnamed: Q2.2, R3.2
unnamed: Q3.1, Q4.3, R11.1
unnamed: Q4.2, R15.1, R20.2
unnamed: Q5.2, R28.2
unnamed: R1.2, U2.7, U2.9
unnamed: R10.1, U7.7, Y1.3
unnamed: R10.2, U7.8, Y1.1
unnamed: R12.1, U8.6
unnamed: R12.2, U9.21
unnamed: R13.2, U9.7
unnamed: R14.1, U9.31
unnamed: R18.1, R22.2, U7.22
unnamed: R19.1, U9.26
unnamed: R23.1, U7.2
unnamed: R24.1, U7.11
unnamed: R25.1, U9.13
unnamed: R32.2, U10.1
unnamed: U3.2, U4.24
unnamed: U3.3, U4.23
unnamed: U8.1, U9.20

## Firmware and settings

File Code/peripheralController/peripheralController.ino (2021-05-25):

// Board: Arduino Pro / Pro Mini
// enable additional analog pins

#include <Wire.h>

#define LED4 8
#define LED3 MISO
#define LED2 MOSI
#define LED1 SCK
#define PWR_EN 14
#define MOTOR_EN 4
#define RIGHT_FORWARD 9
#define RIGHT_BACK 10
#define LEFT_FORWARD 5
#define LEFT_BACK 6

// SERVOS 0123 ARE PC0123

#define PULSE_MAX 2000

uint16_t servo1 = 1000, servo2 = 1000, servo3 = 1000, servo4 = 1000;
byte servo_tick = 0;
byte ir_trigger = 0;
bool lockdown = 0;

void showBatteryLevel(byte level) {
  digitalWrite(LED4, 0);
  digitalWrite(LED3, 0);
  digitalWrite(LED2, 0);
  digitalWrite(LED1, 0);
  switch(level){
    case 4:
      digitalWrite(LED4, 1);
    case 3:
      digitalWrite(LED3, 1);
    case 2:
      digitalWrite(LED2, 1);
    case 1:
      digitalWrite(LED1, 1);
      break;
  }
}

void writeMotors(int8_t left, int8_t right) {
  if(left > 0) {
    digitalWrite(LEFT_BACK, 0);
    analogWrite(LEFT_FORWARD, left << 1);
  } else if(left < 0) {
    digitalWrite(LEFT_FORWARD, 0);
    analogWrite(LEFT_BACK, left << 1);
  } else {
    digitalWrite(LEFT_FORWARD, 0);
    digitalWrite(LEFT_BACK, 0);
  }
  
  if(right > 0) {
    digitalWrite(RIGHT_BACK, 0);
    analogWrite(RIGHT_FORWARD, right << 1);
  } else if(right < 0) {
    digitalWrite(RIGHT_FORWARD, 0);
    analogWrite(RIGHT_BACK, right << 1);
  } else {
    digitalWrite(RIGHT_FORWARD, 0);
    digitalWrite(RIGHT_BACK, 0);
  }
}

//interrupt occurs with 100.24 hz frequency, must be nonblocking because micros is used
ISR(TIMER2_COMPA_vect, ISR_NOBLOCK){
  servo_tick = 1 - servo_tick;
  if(servo_tick) { //do the servo pulse every other isr
    unsigned long loop_timer = micros();
    unsigned long difference;
    // Motor pins high
    PORTC |= 0x0F;
    byte i = 0x0F;
    
    while(i) {
      difference = micros() - loop_timer;
      
      if ((0b00000001 & i) && difference >= servo1) {
        PORTC &= 0b11111110;
        i &= 0b11111110;
      } 
      if ((0b00000010 & i) && difference >= servo2) {
        PORTC &= 0b11111101;
        i &= 0b11111101;
      } 
      if ((0b00000100 & i) && difference >= servo3) {
        PORTC &= 0b11111011;
        i &= 0b11111011;
      } 
      if ((0b00001000 & i) && difference >= servo4) {
        PORTC &= 0b11110111;
        i &= 0b11110111;
      } 
      if(difference >= PULSE_MAX) {
        // shutoff all servo pins
        PORTC &= 0xF0;
        break;
      }
    }
  }
}

ISR(INT0_vect) { //Interrupt from IR receiver
  ir_trigger++;
  if(ir_trigger > 5) {
    lockdown = 1;
  }
}

ISR(INT1_vect) { //Interrupt from motor controller
  digitalWrite(MOTOR_EN, 0); // shutoff motors until restart
}

void setup() {
  // put your setup code here, to run once:
  pinMode(LED4, OUTPUT);
  pinMode(LED3, OUTPUT);
  pinMode(LED2, OUTPUT);
  pinMode(LED1, OUTPUT);
  pinMode(PWR_EN, OUTPUT);
  pinMode(MOTOR_EN, OUTPUT);
  digitalWrite(PWR_EN, 1);
  digitalWrite(MOTOR_EN, 1);
  ir_trigger = 0;
  lockdown = 0;

  // TIMER 2 for interrupt frequency 100 Hz:
  noInterrupts(); // stop interrupts
  TCCR2A = 0; // set entire TCCR2A register to 0
  TCCR2B = 0; // same for TCCR2B
  TCNT2  = 0; // initialize counter value to 0
  // set compare match register for 100 Hz increments
  OCR2A = 155; // = 16000000 / (1024 * 100) - 1 (must be <256)
  // turn on CTC mode
  TCCR2A |= _BV(WGM21);
  // Set CS22, CS21 and CS20 bits for 1024 prescaler
  TCCR2B |= _BV(CS22) | _BV(CS21) | _BV(CS20); // divide by 1024 = 15625 hz
  TIFR2 |= _BV(OCF2A);      // clear any pending interrupts;
  TIMSK2 |= _BV(OCIE2A);  // enable the output compare interrupt

  EICRA = 0x0F;  // rising edge on INT0 and INT1 both trigger their respective interrupts
  EIMSK = 0b00000011;   // enable INT0 and INT1 interrupts
  interrupts(); // allow interrupts

  showBatteryLevel(0);
}

void loop() {
  /*if(lockdown) { // needs to receive at least 3 pulses from IR receiver (noise reject)
    digitalWrite(MOTOR_EN, 0); // shutoff motors until restart
    digitalWrite(PWR_EN, 0); // shutoff power until restart
    PORTC &= 0xF0; // shutoff all servos until restart
    writeMotors(0, 0); // shutoff motors until restart
    while(1) { // lockdown into infinite loop
      showBatteryLevel(4);
      delay(250);
      showBatteryLevel(0);
      delay(250);
    }
  }*/

  digitalWrite(MOTOR_EN, 1);
  
  // put your main code here, to run repeatedly:
  showBatteryLevel(0);
  delay(500);
  showBatteryLevel(1);
  delay(500);
  showBatteryLevel(2);
  delay(500);
  showBatteryLevel(3);
  delay(500);
  showBatteryLevel(4);
  delay(500);
  servo1 = 1000;
  servo2 = 1250;
  servo3 = 1500;
  servo4 = 1750;
  
  writeMotors(100, 100);
  delay(1000);
  writeMotors(-100, -100);
  delay(1000);
  
  ir_trigger = 0; //clear this every so often
}

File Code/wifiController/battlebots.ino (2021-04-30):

/*************************************************************
  Download latest Blynk library here:
    https://github.com/blynkkk/blynk-library/releases/latest

  Blynk is a platform with iOS and Android apps to control
  Arduino, Raspberry Pi and the likes over the Internet.
  You can easily build graphic interfaces for all your
  projects by simply dragging and dropping widgets.

    Downloads, docs, tutorials: http://www.blynk.cc
    Sketch generator:           http://examples.blynk.cc
    Blynk community:            http://community.blynk.cc
    Follow us:                  http://www.fb.com/blynkapp
                                http://twitter.com/blynk_app

  Blynk library is licensed under MIT license
  This example code is in public domain.

 *************************************************************

  You’ll need:
   - Blynk App (download from AppStore or Google Play)
   - NodeMCU board
   - Decide how to connect to Blynk
     (USB, Ethernet, Wi-Fi, Bluetooth, ...)

  There is a bunch of great example sketches included to show you how to get
  started. Think of them as LEGO bricks  and combine them as you wish.
  For example, take the Ethernet Shield sketch and combine it with the
  Servo example, or choose a USB sketch and add a code from SendData
  example.
 *************************************************************/

/* Comment this out to disable prints and save space */
#define BLYNK_PRINT Serial


#include <ESP8266WiFi.h>
#include <Servo.h>
#include <BlynkSimpleEsp8266.h>


//BLYNK VALUES
char auth[] = "bwilCptQtp710DQOEdzOXD6tX4ud44DA";
char ssid[] = "";
char pass[] = "";


//PORTS
const uint8_t servoPin = D0;
const uint8_t leftMotorPin1 = D1;
const uint8_t leftMotorPin2 = D2;
const uint8_t rightMotorPin1 = D3;
const uint8_t rightMotorPin2 = D4;
const uint8_t ledPin = D5;

Servo servo;


//SERVO CONTROL
void servoContol(int pinValue) 
{
  servo.write(pinValue);
}


//MOTOR CONTROL
void leftMotorControl(int x)
{
  int dutyCycle = abs(x) * 1023 / 1000;
  if (x > 0) {
    //digitalWrite(leftMotorPin1, HIGH);
    digitalWrite(leftMotorPin2, LOW);
    analogWrite(leftMotorPin1, dutyCycle);
  } else if (x < 0) {
    digitalWrite(leftMotorPin1, LOW);
    //digitalWrite(leftMotorPin2, HIGH);
    analogWrite(leftMotorPin2, dutyCycle);
  }
  else {
    digitalWrite(leftMotorPin1, LOW);
    digitalWrite(leftMotorPin2, LOW);
  }
}

void rightMotorControl(int x)
{
  int dutyCycle = abs(x) * 1023 / 1000;
  if (x > 0) {
    //digitalWrite(rightMotorPin1, HIGH);
    digitalWrite(rightMotorPin2, LOW);
    analogWrite(rightMotorPin1, dutyCycle);
  } else if (x < 0) {
    digitalWrite(rightMotorPin1, LOW);
    //digitalWrite(rightMotorPin2, HIGH);
    analogWrite(rightMotorPin2, dutyCycle);
  }
  else {
    digitalWrite(rightMotorPin1, LOW);
    digitalWrite(rightMotorPin2, LOW);
  }
}



//BLYNK VIRTUAL PORTS
BLYNK_WRITE(V0)
{
  int pinValue = param.asInt();
  Serial.print("V0 Slider value is: ");
  Serial.println(pinValue);
  servoContol(pinValue);
}

BLYNK_WRITE(V1)
{
  int x = param[0].asInt();
  int y = param[1].asInt();

  // Do something with x and y
  Serial.print("Left X = ");
  Serial.print(x);
  Serial.print("; Left Y = ");
  Serial.println(y);

  leftMotorControl(x);
}

BLYNK_WRITE(V2)
{
  int x = param[0].asInt();
  int y = param[1].asInt();

  // Do something with x and y
  Serial.print("Right X = ");
  Serial.print(x);
  Serial.print("; Right Y = ");
  Serial.println(y);

  rightMotorControl(x);
}


void setup()
{
  // Debug console
  Serial.begin(9600);

  Blynk.begin(auth, ssid, pass);
  // You can also specify server:
  //Blynk.begin(auth, ssid, pass, "blynk-cloud.com", 80);
  //Blynk.begin(auth, ssid, pass, IPAddress(192,168,1,100), 8080);

  servo.attach(servoPin);
  servo.write(0);
  pinMode(leftMotorPin1, OUTPUT);
  pinMode(leftMotorPin2, OUTPUT);
  pinMode(rightMotorPin1, OUTPUT);
  pinMode(rightMotorPin2, OUTPUT);
}

void loop()
{
  Blynk.run();
}

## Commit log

2021-04-29 UPLOAD ALL THE THINGS
    [Battlebots Controller BOM.xlsx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]
2021-04-30 prototype code
